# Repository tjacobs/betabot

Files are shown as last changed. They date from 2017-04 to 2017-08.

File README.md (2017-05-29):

# **Betabot**

### An affordable walking biped robot, designed for deep learning research.

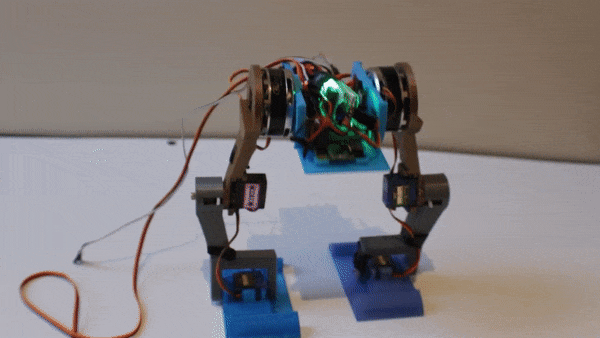
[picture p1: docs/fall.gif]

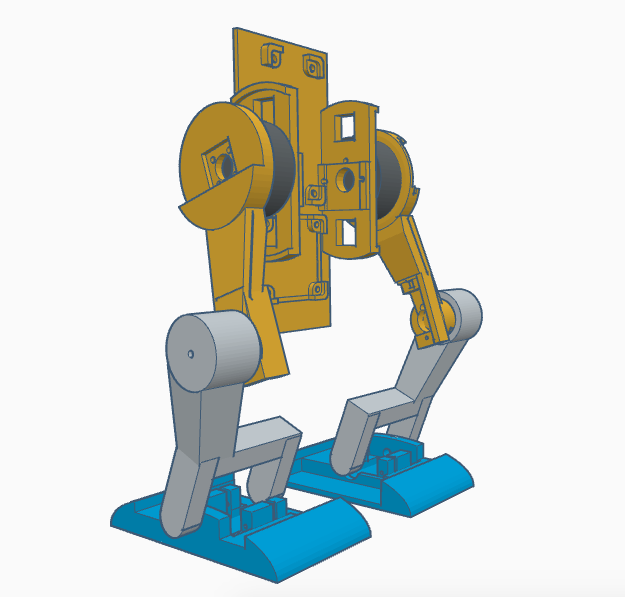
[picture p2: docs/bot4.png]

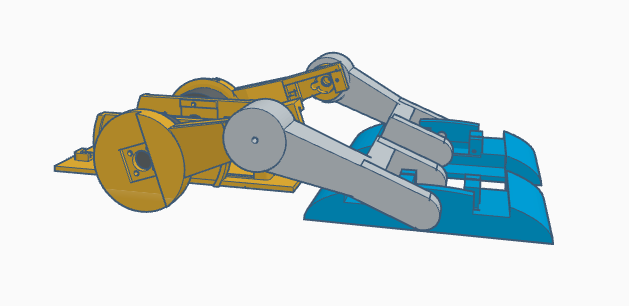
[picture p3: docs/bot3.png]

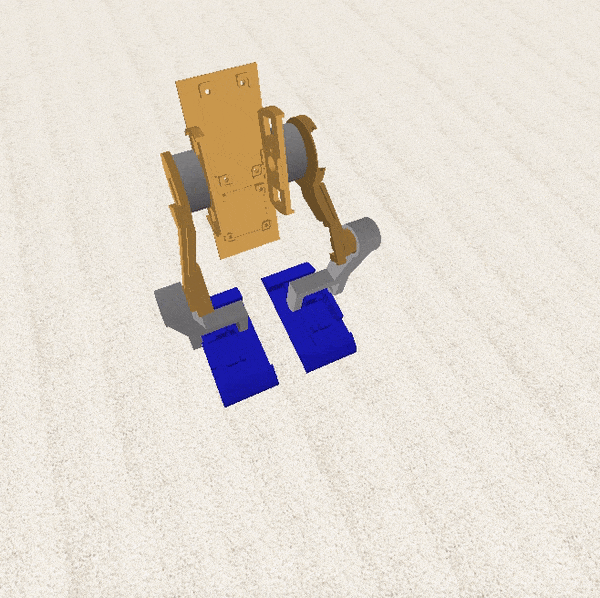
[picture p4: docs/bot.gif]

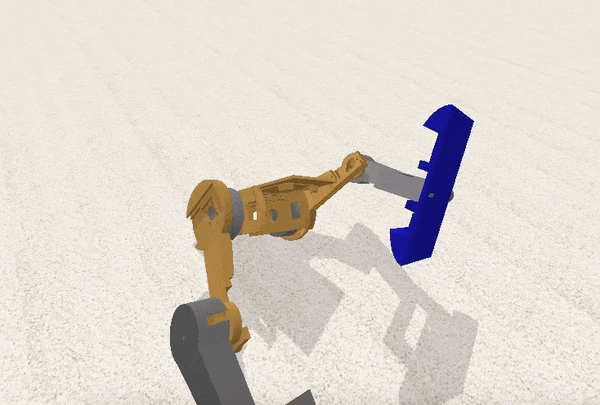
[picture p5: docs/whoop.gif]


**What is it?**
A 3D printed body, Raspberry Pi Zero, motors & motor controllers, sensors, power boards, and a camera.

**What does it run?**
Python, PID loops, OpenCV, TensorFlow, Keras, and Betabot OS running on Raspbian.

**Why?**
To help you simulate and then quickly test out deep learning and computer vision techniques in the real world.

Read more and buy the kit [here](https://robot-overlords.myshopify.com/pages/betabot).

---
### Getting started

Check out the main file: [bot.py](source/bot.py)

Check out the installer: [install](install/install)

Check out the startup help: [welcome](scripts/welcome)

To get started, write the [disk image](coming_soon) using [sd_restore](scripts/sd_restore) and pop it into a Raspberry Pi Zero.

---

### Parts

| Part | US$ |
|--:|--:|
|[BGMC Speed Controller (x2)](http://www.rovertec.com/products-bgmc2.html)| $100 |
|[Gimbal Motor (x2)](https://www.aliexpress.com/item/Maytech-4180-130-turn-rc-brushless-gimbal-motor-in-radio-controlled-toys/1000001024913.html)| $40 |
|[Rotary Encoder (x2)](http://au.mouser.com/Search/ProductDetail.aspx?qs=Rt6VE0PE%2fOduJIB%252bRfeBZQ%3d%3d)| $40 |
|[High Torque Servos (x4)](https://hobbyking.com/en_us/turnigytm-tgy-s901d-ds-mg-robot-servo-13kg-0-14sec-58g.html)| $40 |
|[SPRacing F3 Evo](https://hobbyking.com/en_us/rjx-sp-racing-f3-evo-flight-controller.html)| $24 |
|[16GB Memory Card](https://www.adafruit.com/product/2693)| $20 |
|[1000mAh 3S Lipo Battery](https://hobbyking.com/en_us/turnigy-1000mah-3s-30c-lipo-pack.html)| $10 |
|[Pi Fisheye Cam](https://www.aliexpress.com/item/Raspberry-Pi-Zero-W-Camera-Module-Night-Vision-Wide-Angle-Fisheye-5MP-Webcam-with-Infrared-IR/32802572768.html) [(Alt)](https://www.aliexpress.com/item/Raspberry-Pi-Zero-Camera-Module-5MP-Camera-Webcam-for-Raspberry-Pi-Zero/32782501654.html)| $10 |
|[Raspberry Pi Zero W](https://www.adafruit.com/product/3400)| $10 |
|[Charger Board](https://hobbyking.com/en_us/hobbykingr-dc-4s-balance-charger-cell-checker-30w-2s-4s.html)| $9 |
|[12V/5V Voltage Regulator](https://hobbyking.com/en_us/matek-mini-power-hub-w-bec-5v-and-12v.html) [(Plug)](https://hobbyking.com/en_us/xt60-to-ec2-losi-battery-adapter-2pcs-bag.html)| $8 |
|[3D Printer Filament](https://hobbyking.com/en_us/colido-3d-printer-filament-1-75mm-pla-500g-spool-white.html)| $5 |
|[Misc: Switch, Wire, Heatshrink, Heatsink, Screws](https://www.adafruit.com/product/1478)| $5 |
|[Tiny MicroUSB OTG](https://www.adafruit.com/product/2910)| $3 |
|[Components: 2 Transistors: BDX53C & BDX54C, 2 Resistors]()| $1 | 

As you can see, the gimbals, encoders, and speed controllers are the main cost. I may replace these with large servos for the first version to keep costs down.

### **Extras**

| Part | US$ |
|--:|--:|
|[Raspberry Pi 3](https://www.adafruit.com/product/3055)| $40 |
|[12V Power Supply](https://www.adafruit.com/product/352)[Adapter](https://www.adafruit.com/product/991)| $25 |
|[Wireless Keyboard and Mouse](https://core-electronics.com.au/wireless-keyboard-and-mouse-for-raspberry-pi.html)| $20 |

You'll also need an HDMI cable and a monitor. And a soldering iron and tools.

---

### 3D body

[STL files](https://github.com/tjacobs/betabot/tree/master/ros/src/betabot_description/urdf)

---

### Videos

[Falling](https://github.com/tjacobs/betabot/blob/master/docs/fall.m4v?raw=true)

[Simulator Crawling](https://github.com/tjacobs/betabot/blob/master/docs/legs.mov?raw=true)

[More](https://github.com/tjacobs/betabot/blob/master/docs/)

---

### How it works

#### Hips

Controlled by motor outputs 1 and 2. The hips keep the bot balanced forward/backward (pitch). We read our IMU pitch value, and our PID movement controller updates the speeds of the motor outputs 1 and 2 to bring us level.

#### Knees

Controlled by motor outputs 3 and 4. Run by servos, these work with hips and feet when raising and lowering.

#### Feet

Controlled by motor outputs 5 and 6. Run by servos, these angle the feet so they don't catch when walking.

---
### Development

The Pi Zero runs the bot. It runs the main bot.py file automatically on startup (via /etc/rc.local). No heavy HDMI cables go into the bot, keeping it mobile and untethered.

The Pi Zero is listening for SSH connections via the wifi network it's on.

I use the Pi 3 on my desktop plugged into a big monitor to SSH into the Pi Zero and update code and restart scripts.

Next up: Mount the Pi Zero filesystem over the network so I can edit files directly in text editor on the desktop Pi 3. 
And after that: The Pi Zero listens to any write of the bot.py file, and every time it is written, it restarts `python bot.py`. So you can just hit save on your desktop editor, and the bot starts reacting with the new code instantly.

---
### How to build it

See parts list above.

Take the 3D printed body, two motors, and six screws. Glue the small magnets onto the back of the motor axles. Place one motor on the side of the body. Rotate until screw holes line up, and screw three screws in half way.

Take one motor sensor board, and slide it into position under the three screws, with chip facing towards and sitting directly under the motor magnet. Screw three screws fully in to hold the motor and board in place. Repeat with the other motor.

Solder the power lead, via the on switch, 5v lead, and speed controllers onto the power board. Take the power board and and place it into the mounting square on the body, and screw it down with four spacing screws

Solder the 8 motor output header pins onto the controller board. Place the controller board on top of the power board, and screw it down.

Take the two speed controller boards and plug the motors into them. Place them down into the body.

Write the Betabot [disk image](coming_soon) to the SD memory card using [sd_restore](scripts/sd_restore), and pop it into the Raspberry Pi. Take the Raspberry Pi and place it on the body, with memory card at the outer edge. Screw down with four screws. Plug in the HDMI adapter, and OTG adapter.

Screw the legs onto the motors, and place the servos into the legs and feet, and screw together. Run the leads through the legs and into the controller.

Switch Betabot on. He should wake up after a minute and come to life!

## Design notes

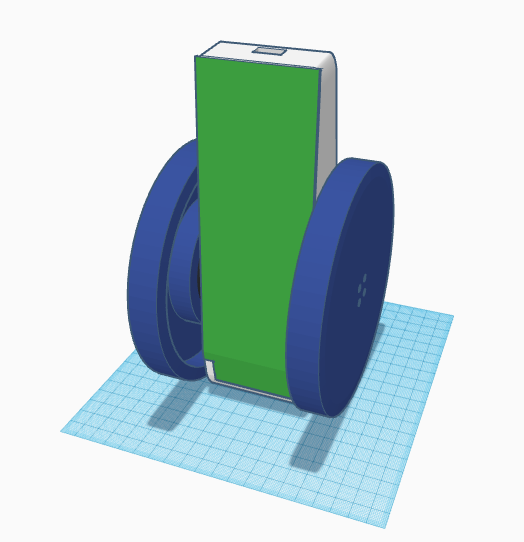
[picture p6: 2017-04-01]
docs/betabot1.png

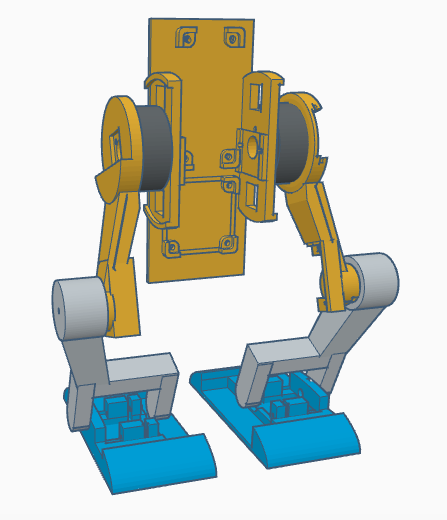
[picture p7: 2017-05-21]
docs/bot2.png

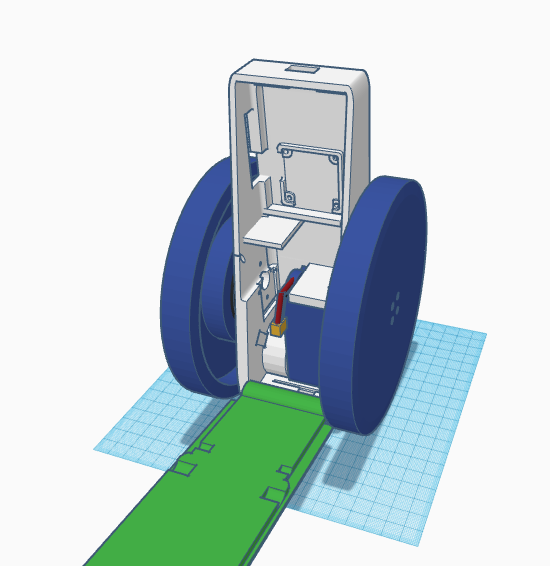
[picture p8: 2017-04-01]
docs/betabot2.png

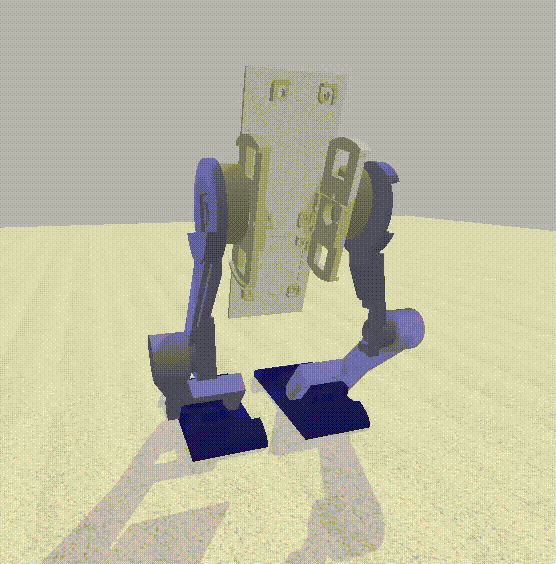
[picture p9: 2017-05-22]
docs/bot3.gif

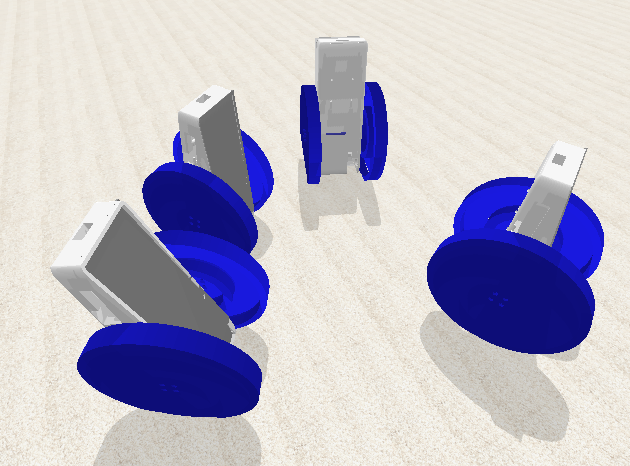
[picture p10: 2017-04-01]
docs/shot2.png

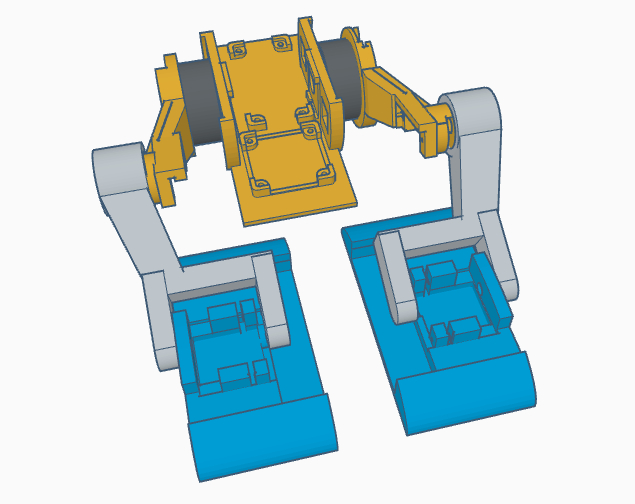
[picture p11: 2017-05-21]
docs/bot.png

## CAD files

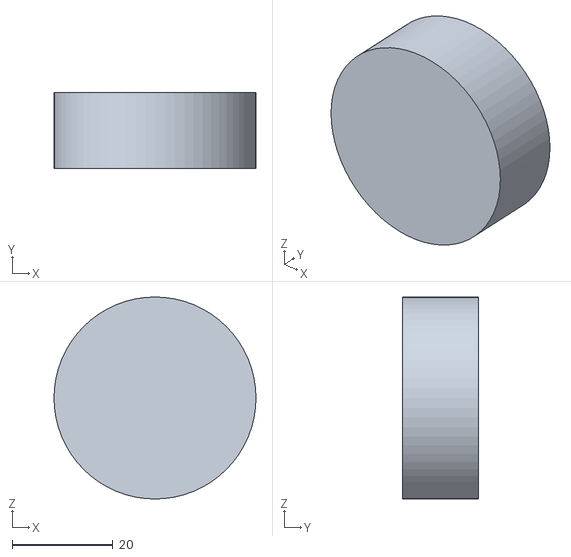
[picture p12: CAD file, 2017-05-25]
ros/src/betabot_description/urdf/right_motor.stl
40.0 x 15.0 x 40.0

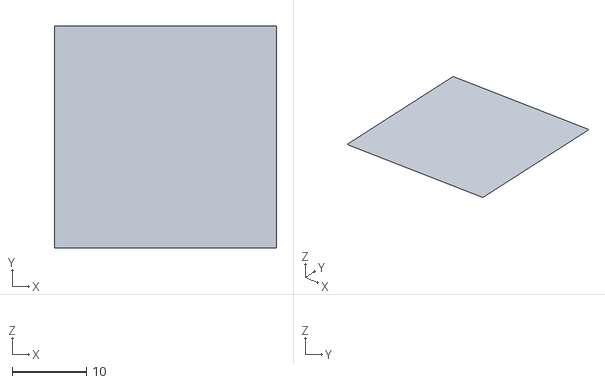
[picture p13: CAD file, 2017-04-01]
simulator/data/plane.obj
30.0 x 30.0 x 0

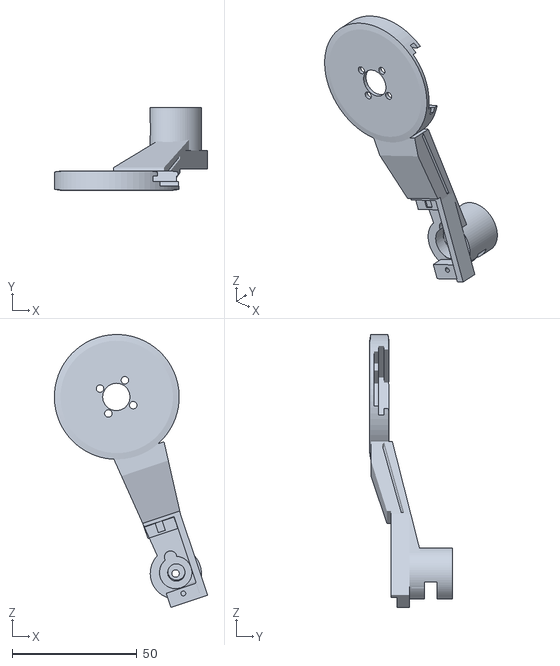
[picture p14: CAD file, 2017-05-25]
ros/src/betabot_description/urdf/right_leg.stl
61.4 x 33.1 x 109.3

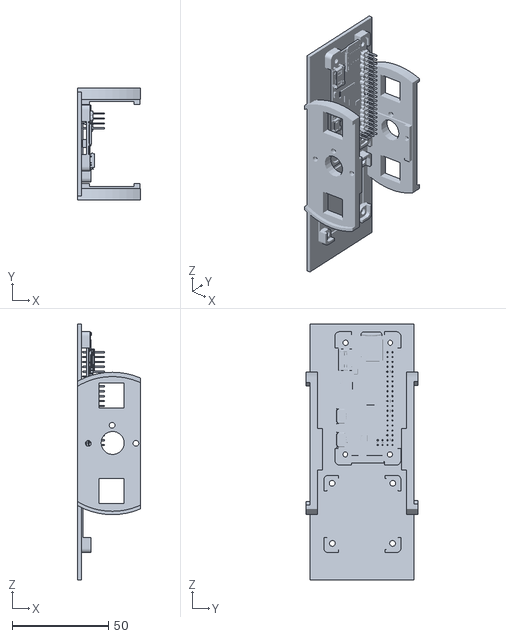
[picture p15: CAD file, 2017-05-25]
ros/src/betabot_description/urdf/body.stl
32.5 x 58.0 x 133.0

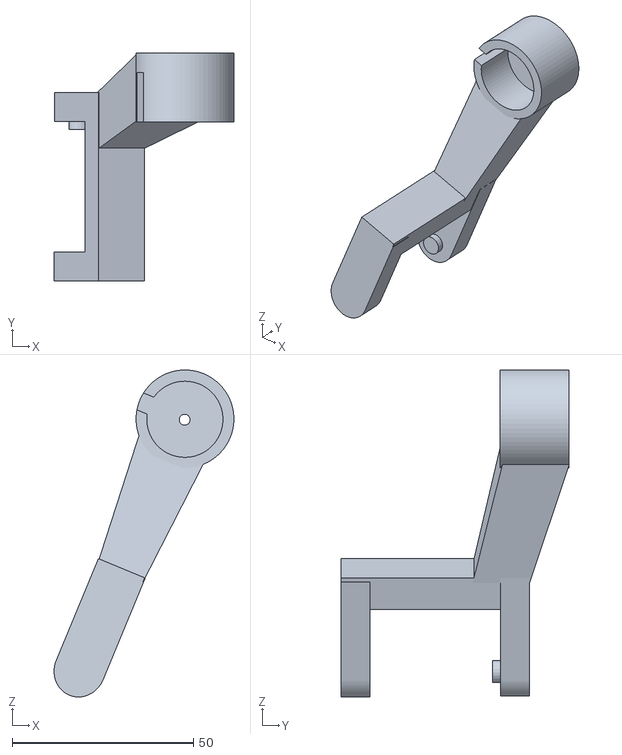
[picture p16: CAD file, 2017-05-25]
ros/src/betabot_description/urdf/right_lower_leg.stl
49.6 x 63.0 x 90.2

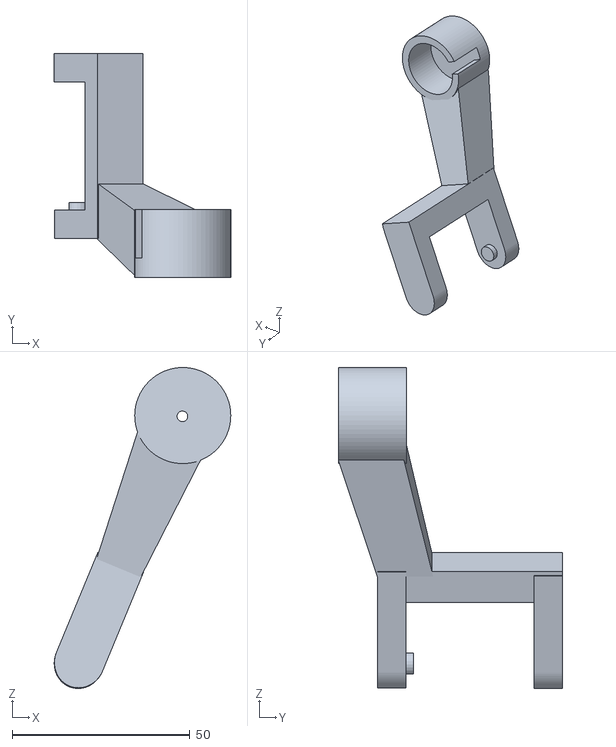
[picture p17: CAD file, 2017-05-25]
ros/src/betabot_description/urdf/left_lower_leg.stl
49.6 x 63.0 x 90.2

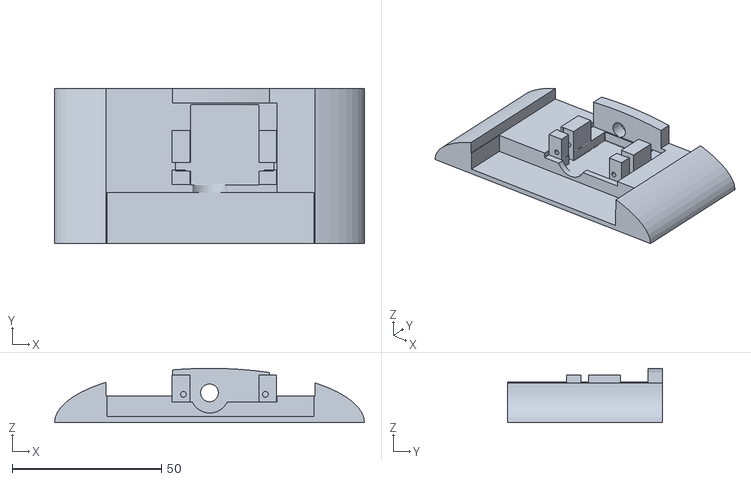
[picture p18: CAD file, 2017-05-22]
ros/src/betabot_description/urdf/right_foot.stl
104.0 x 52.1 x 18.2

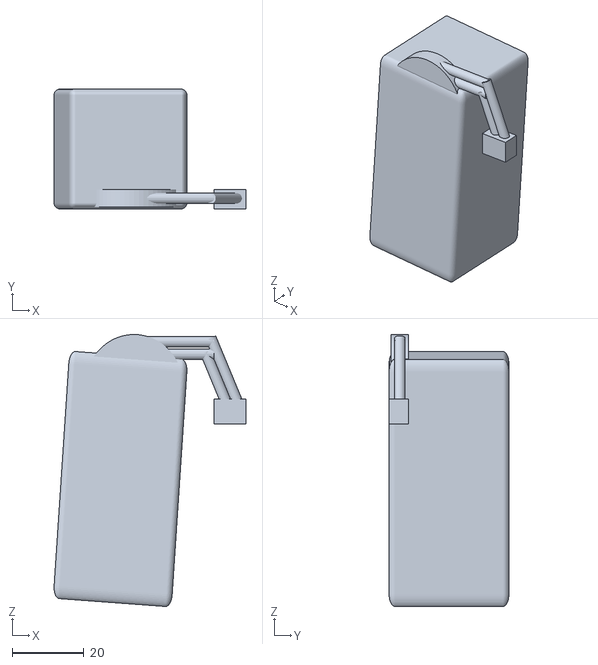
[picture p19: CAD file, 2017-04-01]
ros/src/betabot_description/urdf/battery.stl
53.6 x 33.5 x 76.0

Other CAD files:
ros/src/betabot_description/urdf/left_motor.stl
ros/src/betabot_description/urdf/left_leg.stl
ros/src/betabot_description/urdf/left_foot.stl

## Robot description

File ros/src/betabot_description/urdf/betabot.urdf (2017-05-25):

<?xml version="1.0"?>

<robot name="betabot">

  <link name='chassis'>
    <pose>0 0 0 0 0 0</pose>
    <inertial>
      <mass value="1"/>
      <origin xyz="0 0 0" rpy=" 0 0 0"/>
      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
    </inertial>
    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
  </link>

  <link name="left_foot">
    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
    <inertial>
      <origin xyz="0 0 0" rpy="0 0 0"/>
      <mass value="0.1"/>
      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
    </inertial>
  </link>

  <link name="right_foot">
    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
    <inertial>
      <origin xyz="0 0 0" rpy="0 0 0"/>
      <mass value="0.1"/>
      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
    </inertial>
  </link>

  <link name="right_motor">
    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
    <inertial>
      <origin xyz="0 0 0" rpy="0 0 0"/>
      <mass value="0.8"/>
      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
    </inertial>
  </link>

  <link name="left_motor">
    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
    <inertial>
      <origin xyz="0 0 0" rpy="0 0 0"/>
      <mass value="0.8"/>
      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
    </inertial>
  </link>

  <link name="right_leg">
    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
    <inertial>
      <origin xyz="0 0 0" rpy="0 0 0"/>
      <mass value="0.1"/>
      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
    </inertial>
  </link>

  <link name="left_leg">
    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
    <inertial>
      <origin xyz="0 0 0" rpy="0 0 0"/>
      <mass value="0.1"/>
      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
    </inertial>
  </link>

  <link name="right_lower_leg">
    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
    <inertial>
      <origin xyz="0 0 0" rpy="0 0 0"/>
      <mass value="0.1"/>
      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
    </inertial>
  </link>

  <link name="left_lower_leg">
    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
    <inertial>
      <origin xyz="0 0 0" rpy="0 0 0"/>
      <mass value="0.1"/>
      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
    </inertial>
  </link>


  <joint type="continuous" name="left_motor_joint">
    <origin xyz="0 0 0" rpy="0 0 0"/>
    <parent link="chassis"/>
    <child link="left_motor"/>
    <axis xyz="0 1 0" rpy="0 0 0"/>
    <limit effort="10" velocity="10"/>
    <joint_properties damping="0.5" friction="0.5"/>
  </joint>

  <joint type="continuous" name="right_motor_joint">
    <origin xyz="0 0 0" rpy="0 0 0"/>
    <parent link="chassis"/>
    <child link="right_motor"/>
    <axis xyz="0 1 0" rpy="0 0 0"/>
    <limit effort="10" velocity="10"/>
    <joint_properties damping="0.5" friction="0.5"/>
  </joint>

  <joint type="continuous" name="left_hip_joint">
    <origin xyz="0 0 0" rpy="0 0 0"/>
    <parent link="chassis"/>
    <child link="left_leg"/>
    <axis xyz="0 1 0" rpy="0 0 0"/>
    <limit effort="10" velocity="10"/>
    <joint_properties damping="0.5" friction="0.5"/>
  </joint>

  <joint type="continuous" name="right_hip_joint">
    <origin xyz="0 0 0" rpy="0 0 0"/>
    <parent link="chassis"/>
    <child link="right_leg"/>
    <axis xyz="0 1 0" rpy="0 0 0"/>
    <limit effort="10" velocity="10"/>
    <joint_properties damping="0.5" friction="0.5"/>
  </joint>

  <joint type="continuous" name="left_knee_joint">
    <origin xyz="0.25 0 -0.7" rpy="0 0 0"/>
    <parent link="left_leg"/>
    <child link="left_lower_leg"/>
    <axis xyz="0 1 0" rpy="0 0 0"/>
    <limit effort="10" velocity="10"/>
    <joint_properties damping="0.5" friction="0.5"/>
  </joint>

  <joint type="continuous" name="right_knee_joint">
    <origin xyz="0.25 0 -0.7" rpy="0 0 0"/>
    <parent link="right_leg"/>
    <child link="right_lower_leg"/>
    <axis xyz="0 1 0" rpy="0 0 0"/>
    <limit effort="10" velocity="10"/>
    <joint_properties damping="0.5" friction="0.5"/>
  </joint>

  <joint type="continuous" name="left_foot_joint">
    <origin xyz="-0.5 0 -0.7" rpy="0 0 0"/>
    <parent link="left_lower_leg"/>
    <child link="left_foot"/>
    <axis xyz="0 1 0" rpy="0 0 0"/>
    <limit effort="10" velocity="10"/>
    <joint_properties damping="0.5" friction="0.5"/>
  </joint>

  <joint type="continuous" name="right_foot_joint">
    <origin xyz="-0.5 0 -0.7" rpy="0 0 0"/>
    <parent link="right_lower_leg"/>
    <child link="right_foot"/>
    <axis xyz="0 1 0" rpy="0 0 0"/>
    <limit effort="10" velocity="10"/>
    <joint_properties damping="0.5" friction="0.5"/>
  </joint>

</robot>

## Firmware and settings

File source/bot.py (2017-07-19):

# Betabot
# https://github.com/tjacobs/betabot
# by Tom Jacobs

print( "Starting Betabot." )

# Imports
import sys
import time
import math
import array
import datetime
import functions
import motors as motorsModule
import walk
import sensors

#import remote

import letsrobot_controller
import letsrobot_video

# OSC
#from pythonosc import osc_message_builder
#from pythonosc import udp_client

# What shall we enable?
ENABLE_KEYS 		= True
ENABLE_MOUSE 		= True
ENABLE_BRAIN 		= False
ENABLE_SIMULATOR 	= False

# Import Betabot parts
keys 		= None
mouse 		= None
brain 		= None
simulator 	= None
if ENABLE_KEYS:
	import keys
if ENABLE_MOUSE:
	import mouse
if ENABLE_BRAIN:
	import brain
if ENABLE_SIMULATOR:
	sys.path.append( 'simulator' )
	import simulator

# Go
def main():
	# Flush output for file logging
	sys.stdout.flush()

	# Init motor angle sensors via I2C
	magneticSensors = sensors.AMS()
	magneticSensors.connect(1)
	
	# Init motors via USB
	motorsModule.initMotors()
	motors = [0.0] * 9 # Motor outputs 1 to 8, ignore 0

	# Motor speeds
	speed_left = 0.0
	speed_right = 0.0
	
	# Remote control
	old_remote_x = 0.0
	old_remote_y = 0.0

	# Wait on other threads to start up
	time.sleep(0.5)
	
	# Send OSC commands
#	ip = "192.168.4.1"
#	port = 2222
#	client = udp_client.SimpleUDPClient(ip, port)

	# Loop
	while not keys or not keys.esc_key_pressed:

		# Read current accelerometer value to see how far forward we're leaning
		pitch = motorsModule.readIMU('ax')

		# Read battery level
		voltage = 0#motorsModule.readBatteryVoltage()

		# Read current angles of motors
		currentAngles = functions.readCurrentAngles(magneticSensors)
		
		# Calculate difference in mouse x position
		try:
			diff_x = remote.x - old_remote_x
			diff_y = remote.y - old_remote_y
			old_remote_x = remote.x
			old_remote_y = remote.y
		except NameError:
			pass

		FORWARD_SPEED = 2.0
		BACKWARD_SPEED = 2.0
		TURNING_SPEED = 4.0
		MOVEMENT_SPEED = 4.0

		# Remote
		try:
			# Change motor speeds for turning left right
			speed_left -= diff_x * TURNING_SPEED / 100.0
			speed_right += diff_x * TURNING_SPEED / 100.0

			# Remote keyboard commands
			if remote.up:
				speed_left = speed_left - FORWARD_SPEED
				speed_right = speed_right - FORWARD_SPEED
			if remote.down:
				speed_left = speed_left + BACKWARD_SPEED
				speed_right = speed_right + BACKWARD_SPEED
			if remote.left:
				speed_left += 20.0
				speed_right -= 20.0
			if remote.right:
				speed_left -= 20.0
				speed_right += 20.0
			
			# Go forward backward on mouse y
			speed_left += diff_y * MOVEMENT_SPEED / 100.0
			speed_right += diff_y * MOVEMENT_SPEED / 100.0
			
			# Go foward backward on clicks
			if remote.left_mouse_down:
				speed_left = speed_left - FORWARD_SPEED
				speed_right = speed_right - FORWARD_SPEED
			if remote.right_mouse_down:
				speed_left = speed_left + BACKWARD_SPEED
				speed_right = speed_right + BACKWARD_SPEED

		except NameError:
			pass

		# Let's Robot controller
		try:
			if letsrobot_controller.forward:
				speed_left = speed_left - FORWARD_SPEED
				speed_right = speed_right - FORWARD_SPEED
			if letsrobot_controller.backward:
				speed_left = speed_left + BACKWARD_SPEED
				speed_right = speed_right + BACKWARD_SPEED
			if letsrobot_controller.left:
				speed_left += 1.0 * TURNING_SPEED / 5.0
				speed_right -= 1.0 * TURNING_SPEED / 5.0
			if letsrobot_controller.right:
				speed_left -= 1.0 * TURNING_SPEED / 5.0
				speed_right += 1.0 * TURNING_SPEED / 5.0
		except NameError:
			pass

		# Clamp
		speed_left = functions.clamp( speed_left, -100, 100)
		speed_right = functions.clamp( speed_right, -100, 100)

		# Send to BROBOT
#		client.send_message("/1/fader1", 0.5 + speed_left/400.0 + speed_right/400.0)
#		client.send_message("/1/fader2", 0.5 + speed_left/500.0 - speed_right/500.0)

		# Balance
		targetAngles = [None, 0, 0]
		targetAngles[1] = - pitch - 22 - speed_left/2
		targetAngles[2] = - pitch - 22 - speed_right/2

		# Run movement controller to see how fast we should set our motor speeds
		movement = walk.calculateMovement(currentAngles, targetAngles)

		# Send motor commands
		motors[1] = 0#movement[1] 	 # Right motor
		motors[2] = 0#movement[2] 	 # Left motor
		motors[1] = speed_right/5	     # Right motor
		motors[2] = speed_left/5   	 # Left motor
		motorsModule.sendMotorCommands(motors, simulator, False, True)

		# Display balance, angles, target angles and speeds
#		functions.display( "Pitch: %3d. Right, Left: Hips: %3d, %3d, Targets: %3d, %3d, Speeds: %3d, %3d.  %3d %3d" 
#		        % (pitch, currentAngles[1], currentAngles[2], targetAngles[1], targetAngles[2], motors[1], motors[2], speed_left, speed_right ) )
		#functions.display( "Pitch: %3d. Right, Left: Knees: %3d, %3d, Targets: %3d, %3d, Speeds: %3d, %3d" 
		#        % (pitch, 0, 0, targetAngles[3], targetAngles[4], motors[3], motors[4] ) )
#		functions.display( "Pitch: %3d. Right, Left: Feet: %3d, %3d, Targets: %3d, %3d, Speeds: %3d, %3d" 
#		        % (pitch, 0, 0, targetAngles[5], targetAngles[6], motors[5], motors[6] ) )

		# Slow down
		speed_left = speed_left * 0.94
		speed_right = speed_right * 0.94


	# Stop motors
	motorsModule.stopMotors()

# Go
if __name__=="__main__":
   main()

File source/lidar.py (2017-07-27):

#Display Data from Neato LIDAR
#based on code from Nicolas "Xevel" Saugnier
#requires vpython and pyserial


import thread, time, sys, traceback, math

com_port = "/dev/serial0" # example: 5 == "COM6" == "/dev/tty5"
baudrate = 115200
visualization = True

offset = 140
init_level = 0
index = 0

lidarData = [[] for i in range(360)] #A list of 360 elements Angle, Distance , quality


if visualization:
    from visual import *
# sample and intensity points
    point = points(pos=[(0,0,0) for i in range(360)], size=5, color=(0 , 1, 0))
    pointb = points(pos=[(0,0,0) for i in range(360)], size=5, color=(0.4, 0, 0))
    point2 = points(pos=[(0,0,0) for i in range(360)], size=3, color=(1 , 1, 0))
    point2b = points(pos=[(0,0,0) for i in range(360)], size=3, color=(0.4, 0.4, 0))
    #lines
    outer_line= curve (pos=[(0,0,0) for i in range(360)], size=5, color=(1 , 0, 0))
    lines=[curve(pos=[(offset*cos(i* pi / 180.0),0,offset*-sin(i* pi / 180.0)),(offset*cos(i* pi / 180.0),0,offset*-sin(i* pi / 180.0))], color=[(0.1, 0.1, 0.2),(1,0,0)]) for i in range(360)]
    zero_intensity_ring = ring(pos=(0,0,0), axis=(0,1,0), radius=offset-1, thickness=1, color = color.yellow)

    label_speed = label(pos = (0,-500,0), xoffset=1, box=False, opacity=0.1)
    label_errors = label(pos = (0,-1000,0), xoffset=1, text="errors: 0", visible = False, box=False)

use_points = True
use_outer_line = False
use_lines = False
use_intensity = True

def update_view( angle, data ):
    """Updates the view of a sample.

Takes the angle (an int, from 0 to 359) and the list of four bytes of data in the order they arrived.
"""
    global offset, use_outer_line, use_line
    #unpack data using the denomination used during the discussions
    x = data[0]
    x1= data[1]
    x2= data[2]
    x3= data[3]
    
    angle_rad = angle * math.pi / 180.0
    c = math.cos(angle_rad)
    s = -math.sin(angle_rad)

    dist_mm = x | (( x1 & 0x3f) << 8) # distance is coded on 13 bits ? 14 bits ?
    quality = x2 | (x3 << 8) # quality is on 16 bits
    lidarData[angle] = [dist_mm,quality]
    dist_x = dist_mm*c
    dist_y = dist_mm*s
    if visualization:
        #reset the point display
        point.pos[angle] = vector( 0, 0, 0 )
        pointb.pos[angle] = vector( 0, 0, 0 )
        point2.pos[angle] = vector( 0, 0, 0 )
        point2b.pos[angle] = vector( 0, 0, 0 )
        if not use_lines : lines[angle].pos[1]=(offset*c,0,offset*s)
        if not use_outer_line :
            outer_line.pos[angle]=(offset*c,0,offset*s)
            outer_line.color[angle] = (0.1, 0.1, 0.2)
        
        
        # display the sample
        if x1 & 0x80: # is the flag for "bad data" set?
            # yes it's bad data
            lines[angle].pos[1]=(offset*c,0,offset*s)
            outer_line.pos[angle]=(offset*c,0,offset*s)
            outer_line.color[angle] = (0.1, 0.1, 0.2)
        else:
            # no, it's cool
            if not x1 & 0x40:
                # X+1:6 not set : quality is OK
                if use_points : point.pos[angle] = vector( dist_x,0, dist_y)
                if use_intensity : point2.pos[angle] = vector( (quality + offset)*c,0, (quality + offset)*s)
                if use_lines : lines[angle].color[1] = (1,0,0)
                if use_outer_line : outer_line.color[angle] = (1,0,0)
            else:
                # X+1:6 set : Warning, the quality is not as good as expected
                if use_points : pointb.pos[angle] = vector( dist_x,0, dist_y)
                if use_intensity : point2b.pos[angle] = vector( (quality + offset)*c,0, (quality + offset)*s)
                if use_lines : lines[angle].color[1] = (0.4,0,0)
                if use_outer_line : outer_line.color[angle] = (0.4,0,0)
            if use_lines : lines[angle].pos[1]=( dist_x, 0, dist_y)
            if use_outer_line : outer_line.pos[angle]=( dist_x, 0, dist_y)




def checksum(data):
    """Compute and return the checksum as an int.

data -- list of 20 bytes (as ints), in the order they arrived in.
"""
    # group the data by word, little-endian
    data_list = []
    for t in range(10):
        data_list.append( data[2*t] + (data[2*t+1]<<8) )
    
    # compute the checksum on 32 bits
    chk32 = 0
    for d in data_list:
        chk32 = (chk32 << 1) + d

    # return a value wrapped around on 15bits, and truncated to still fit into 15 bits
    checksum = (chk32 & 0x7FFF) + ( chk32 >> 15 ) # wrap around to fit into 15 bits
    checksum = checksum & 0x7FFF # truncate to 15 bits
    return int( checksum )


def gui_update_speed(speed_rpm):
    label_speed.text = "RPM : " + str(speed_rpm)

def compute_speed(data):
    speed_rpm = float( data[0] | (data[1] << 8) ) / 64.0
    return speed_rpm
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

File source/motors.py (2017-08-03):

# -------------
# Motor functions
import time
import sys
import functions
import math

# Motor speeds can go from -100 to 100
def clampMotorSpeeds(motorSpeeds):
	minSpeed = -100.0
	maxSpeed = 100.0
	for i in range(len(motorSpeeds)):
		motorSpeeds[i] = functions.clamp(motorSpeeds[i], minSpeed, maxSpeed)
	return motorSpeeds

# Read IMU
def readIMU(xy='ax'):
	global board
	if board == None:
		return 0
	board.getData(MultiWii.RAW_IMU)
	return 90.0 * board.rawIMU[xy] / 500.0 # Pitch

# Read battery voltage
def readBatteryVoltage():
	global board
	if board == None:
		return 0
	board.getData(MultiWii.ANALOG)
	return board.batteryVoltage

# Init
simulator = None
motorEnablePin = 18 # Broadcom 18 = pin 12, 6 from the top corner on the outside of the Pi
goTime = 0
MultiWii = None
board = None
sineOffset = 0
try:
	from controller_board import MultiWii
except:
	print("ERROR initing")
	pass

# Init motors
def initMotors():
	global board
	try:
		board = MultiWii("/dev/ttyACM1")
	except:
		try:
			board = MultiWii("/dev/ttyUSB0")
		except:
			try:
				board = MultiWii("/dev/ttyACM0")
			except:
				print( "\nError: Cannot access USB motors." )
				sys.stdout.flush()

	# Motor enable pin
	try:
		import RPi.GPIO as GPIO
		GPIO.setwarnings(False)
		GPIO.setmode(GPIO.BCM)
		GPIO.setup(motorEnablePin, GPIO.OUT)
		GPIO.output(motorEnablePin, GPIO.LOW)

		# Test
		if( False ):
			time.sleep( 0.2 )
			sys.stdout.write("\r\x1b[KTest: Motors on." )
			GPIO.output(motorEnablePin, GPIO.HIGH)
			time.sleep( 2 )
			sys.stdout.write("\r\x1b[KTest: Motors off." )
			GPIO.output(motorEnablePin, GPIO.LOW)
			time.sleep( 1 )
			sys.stdout.write("\n" )

	except:
		print( "Error: Cannot access GPIO." )
		print( sys.exc_info() )
		sys.stdout.flush()

def stopMotors():
	global board
	motorSpeeds = [0.0] * 9
	motorSpeeds[1] = 0
	motorSpeeds[2] = 0
	sendMotorCommands(motorSpeeds)
	board.close()

	# Finish up
	try:
		import RPi.GPIO as GPIO
		GPIO.cleanup()
	except:
		pass

go = False
# Send the motor speeds to the motors, and enable the motors if any have any speed
def sendMotorCommands(motorSpeedsIn, simulator=None, displayChannels=False, displayCommands=False):
	global goTime, board, motorEnablePin, go, sineOffset
	motorSpeeds = [0.0] * 9
	
	
	# Any motor speeds?
	for i in range(len(motorSpeedsIn)):
		motorSpeeds[i] = motorSpeedsIn[i]
		if motorSpeeds[i] > 2 or motorSpeeds[i] < -2:
			# Set used time as now
#			if go == False:
#				time.sleep( 2 )
			go = True
			goTime = time.time()*1000

	# Leave disabled
	if False:
		# Test all motor commands
		sineOffset += 10.0
		motorSpeeds[1] = math.sin(sineOffset/100.0)*100.0 # Right hip
		motorSpeeds[2] = math.sin(sineOffset/100.0)*100.0 # Left hip
		motorSpeeds[3] = math.sin(sineOffset/100.0)*100.0 # Right knee servo
		motorSpeeds[4] = math.sin(sineOffset/100.0)*100.0 # Left knee servo
		motorSpeeds[5] = math.sin(sineOffset/100.0)*100.0 # Right foot servo
		motorSpeeds[6] = math.sin(sineOffset/100.0)*100.0 # Left foot servo
		motorSpeeds[7] = math.sin(sineOffset/100.0)*100.0 # Unused
		motorSpeeds[8] = math.sin(sineOffset/100.0)*100.0 # Unused
			
	# Motors been on for two seconds unused?
	if time.time()*1000 > goTime + 2000:
		go = False

	# Display?
	if( displayCommands ):
		functions.display( "Motors: %3d, %3d, %1f, %1f, %1f, %1f" % (motorSpeeds[1], motorSpeeds[2], motorSpeeds[3], motorSpeeds[4], motorSpeeds[5], motorSpeeds[6] ) )

	# Send
	middle = 1000.0 + 500.0 #+ 5
	scale = 5.0
	motorSpeeds = clampMotorSpeeds(motorSpeeds)
	channels = [int(motorSpeeds[1]*scale+middle),
				int(motorSpeeds[2]*scale+middle),
				int(motorSpeeds[4]*scale+middle), # Why be these flipped, betaflight throttle
				int(motorSpeeds[3]*scale+middle),
				int(motorSpeeds[5]*scale+middle),
				int(motorSpeeds[6]*scale+middle),
				int(motorSpeeds[7]*scale+middle),
				int(motorSpeeds[8]*scale+middle)]
	if( displayChannels ):
		functions.display( "Channels: " + str( channels ) )
	try:
		board.sendCMD(16, MultiWii.SET_RAW_RC, channels)
	except Exception as error:
		print( "\n" + str(sys.exc_info()[1]) )
		initMotors()

	# Set enable pin
	try:
		import RPi.GPIO as GPIO
		if( go ):
			GPIO.output(motorEnablePin, GPIO.HIGH)
		else:
			GPIO.output(motorEnablePin, GPIO.LOW)
	except:
		pass

	# Update simulator
	if simulator and simulator.simulator:
		simulator.simulator.simStep(motorSpeeds)

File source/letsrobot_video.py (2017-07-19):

import subprocess
import shlex
import re
import os
import time
import urllib.request, urllib.error, urllib.parse
import platform
import json
import sys
import base64
import random
import argparse
from socketIO_client import SocketIO, LoggingNamespace
from threading import Thread

parser = argparse.ArgumentParser(description='robot control')
#parser.add_argument('camera_id')
parser.add_argument('--video_device_number', default=0, type=int)
parser.add_argument('--kbps', default=50, type=int)
parser.add_argument('--brightness', default=80, type=int, help='camera brightness')
parser.add_argument('--contrast', default=75, type=int, help='camera contrast')
parser.add_argument('--saturation', default=70, type=int, help='camera saturation')
parser.add_argument('--rotate180', default=False, type=bool, help='rotate image 180 degrees')
parser.add_argument('--env', default="prod")
parser.add_argument('--screen-capture', dest='screen_capture', action='store_true') # tells windows to pull from different camera, this should just be replaced with a video input device option
parser.set_defaults(screen_capture=False)
parser.add_argument('--audio-input-device', default='Microphone (HD Webcam C270)') # currently, this option is only used for windows screen capture

args = parser.parse_args()
#print("args", args)

cameraIDAnswer = "88685178" #args.camera_id 
server = "runmyrobot.com"

# Enable raspicam driver in case a raspicam is being used
os.system("sudo modprobe bcm2835-v4l2")
#os.system("uv4l --driver raspicam --auto-video_nr --extension-presence=1")

if args.env == "dev":
    print("using dev port 8122")
    port = 8122
elif args.env == "prod":
    port = 8022
else:
    print("invalid environment")
    sys.exit(0)
    
socketIO = SocketIO(server, port, LoggingNamespace)
print("Connect video to:", server)

def onHandleCameraCommand(*args):
	pass
    #thread.start_new_thread(handle_command, args)
#    print(args)

socketIO.on('command_to_camera', onHandleCameraCommand)

def onHandleTakeSnapshotCommand(*args):
    print("taking snapshot")
    inputDeviceID = streamProcessDict['device_answer']
    snapShot(platform.system(), inputDeviceID)
    with open ("snapshot.jpg", 'rb') as f:
        data = f.read()
    print("emit")
    socketIO.emit('snapshot', {'image':base64.b64encode(data)})
socketIO.on('take_snapshot_command', onHandleTakeSnapshotCommand)

def randomSleep():
    """A short wait is good for quick recovery, but sometimes a longer delay is needed or it will just keep trying and failing short intervals, like because the system thinks the port is still in use and every retry makes the system think it's still in use. So, this has a high likelihood of picking a short interval, but will pick a long one sometimes."""

    timeToWait = random.choice((0.25, 0.25, 0.25, 0.25, 0.25, 0.25, 0.5, 0.5, 0.5, 0.5, 0.5, 0.5, 0.5, 0.5, 5))
#    print("sleeping", timeToWait)
    time.sleep(timeToWait)

def getVideoPort():
    url = 'http://%s/get_video_port/%s' % (server, cameraIDAnswer)
    for retryNumber in range(3):
        try:
#            print("GET", url)
            response = urllib.request.urlopen(url).read()
            break
        except:
            print("could not open url ", url)
            time.sleep(2)
    return json.loads(response.decode( "utf-8" ))['mpeg_stream_port']

def getAudioPort():
    url = 'http://%s/get_audio_port/%s' % (server, cameraIDAnswer)
    for retryNumber in range(3):
        try:
#            print("GET", url)
            response = urllib.request.urlopen(url).read()
            break
        except:
            print("could not open url ", url)
            time.sleep(2)
    return json.loads(response.decode( "utf-8" ))['audio_stream_port']

def runFfmpeg(commandLine):
#    print(commandLine)
    
    my_env = os.environ.copy()
    my_env["LD_PRELOAD"] = "/usr/lib/uv4l/uv4lext/armv6l/libuv4lext.so"
    ffmpegProcess = subprocess.Popen(shlex.split(commandLine), env=my_env)
    return ffmpegProcess
    
def handleDarwin(deviceNumber, videoPort, audioPort):

#    p = subprocess.Popen(["./ffmpeg", "-list_devices", "true", "-f", "qtkit", "-i", "dummy"], stdout=subprocess.PIPE, stderr=subprocess.PIPE)
#    out, err = p.communicate()
#    print(err.decode( "utf-8" ))
#    deviceAnswer = input("Enter the number of the camera device for your robot from the list above: ")
#    commandLine = 'ffmpeg -f qtkit -i %s -f mpeg1video -b 400k -r 30 -s 320x240 http://%s:%s/hello/320/240/' % (deviceAnswer, server, videoPort)
    commandLine = 'ffmpeg -i input.m4v -f mpeg1video -b 400k -r 30 -s 320x240 http://%s:%s/hello/320/240/' % (server, videoPort)    
    print( commandLine )
    process = runFfmpeg(commandLine)

    return {'process': process, 'device_answer': deviceAnswer}
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

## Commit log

2017-02-20 Added lidar
2017-02-26 Add ams sensor
2017-02-27 Two legs moving prototype code
2017-03-26 bot code
    [Body7.stl, Legs7.stl, bot.stl]
2017-03-29 Added robot model
    [betabot.xacro, macros.xacro, materials.xacro]
2017-03-29 A wheely good time
2017-04-01 Holy jesus simulation
    [battery.stl, betabot.urdf, body.stl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]
2017-04-01 So good
    [betabot.urdf]
2017-04-06 Added simulator
    [betabot.urdf]
2017-04-06 Data dir
    [plane.obj, plane.urdf]
2017-04-06 Dance baby dance
    [betabot.urdf]
2017-04-07 Combine simulator and robot
    [betabot.urdf]
2017-04-11 Motor enable pin
2017-04-17 Feat: Add 3D Model
    Adding 3D model for reference.
    [Betabot.stl, Styled.stl, bot.stl]
2017-04-17 Docs: Add 3D design and video links
    Now people can 3D print their own.
2017-04-19 Motor movements
2017-04-20 Camera capture
2017-04-21 Added camera, brain uses it to predict
2017-04-23 Move motor pin
2017-04-23 Rename ros dir
    [battery.stl, betabot.urdf, body.stl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]
2017-04-27 Camera preview
2017-04-30 Remove duck
    [duck.urdf]
2017-04-30 Update 3d model
    [Betabot.stl, Styled.stl, betabot.stl]
2017-05-01 Read IMU
2017-05-01 MSP motors!
2017-05-04 Fixed motors
2017-05-05 Fix install camera
2017-05-07 Update simulator
    [betabot.urdf, body.stl, left_motor.stl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]
2017-05-08 Fix install and add vision
    [vision.py]
2017-05-09 Fixed keyboard, added other library
    [bot.py, keys.py]
2017-05-09 Fixed mouse and keyboard
    [bot.py, keys.py, mouse.py]
2017-05-10 Start, stop, findusb, utils, printing
2017-05-10 Scripts web, motor code
2017-05-12 Add motors module, display function
2017-05-15 Fixed IMU, improved comments
    [bot.py, walk.py]
2017-05-16 Right leg
2017-05-19 Motor outputs 1 to 8, knee servos
2017-05-20 Pitch IMU
2017-05-22 Update with feet, fix float int
    [betabot.urdf, body.stl, foot_left.stl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]
2017-05-22 Silence hips, colours
    [betabot.urdf]
2017-05-24 x pitch
2017-05-24 Fix magnetic sensors
2017-05-24 Legs hips
2017-05-25 Sim legs!
    [betabot.urdf, body.stl, left_leg.stl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]
2017-05-25 Leg vids
2017-05-25 Fixed feet
    [betabot.urdf]
2017-05-26 All legs
2017-05-26 New assembly instructions
2017-06-16 back to wheels
2017-06-20 Python threads man
2017-06-22 fix motors stop
2017-07-03 Add battery voltage, not working yet
    [bot.py, motors.py, walk.py]
2017-07-14 XV lidar
